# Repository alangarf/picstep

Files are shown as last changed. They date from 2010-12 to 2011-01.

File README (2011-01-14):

Firstly thanks for looking at my design, it was started from the ground up for
the community to share and use. I've released all code and designs under GPL,
which means it's free to use for any purpose as long as my copyright is
retained and any modifications are also released publicly. Any commercial
interest must be approved by ME! :)

PICStep is a micro-stepping step motor controller that uses a special set of
driver ICs (LMD18245) to control the motor coils current to such a degree that
you can divide the magnetic steps of a step motor to 1/2, 1/4, 1/8th or even 1/16th
their original size! Of course resolution suffers a little in 1/16th mode as not
all steps are mechanically identical from one to another; the difference
is negligible, but the increased smoothness and efficiency is dramatic!

PICStep uses a single layer board and about 30 components and a few wire links
to make it all happen.

The LMD18245 are rated at 55V @ 3amps but I've not tested it up to that range
and there are special requirements that need to be met to deal with back EMF
at this range. I'd suggest reading the LMD18245 data-sheet (which is available
freely on the net') if you wish to use these drivers at or near this voltage.

I've tested PICStep at 40VDC @ 2.5A without any modification or problems, but your
mileage may vary! :)

I use a simple 24V toroidal transformer and bridge rectifier for my PSU. 24V
RMS works out to about 35VDC when rectified. Plus I've provided massive amounts
of filtering by using a very large electrolytic capacitor to filter out the humps
and bumps. It works very well and can supply my three drivers without a problem.

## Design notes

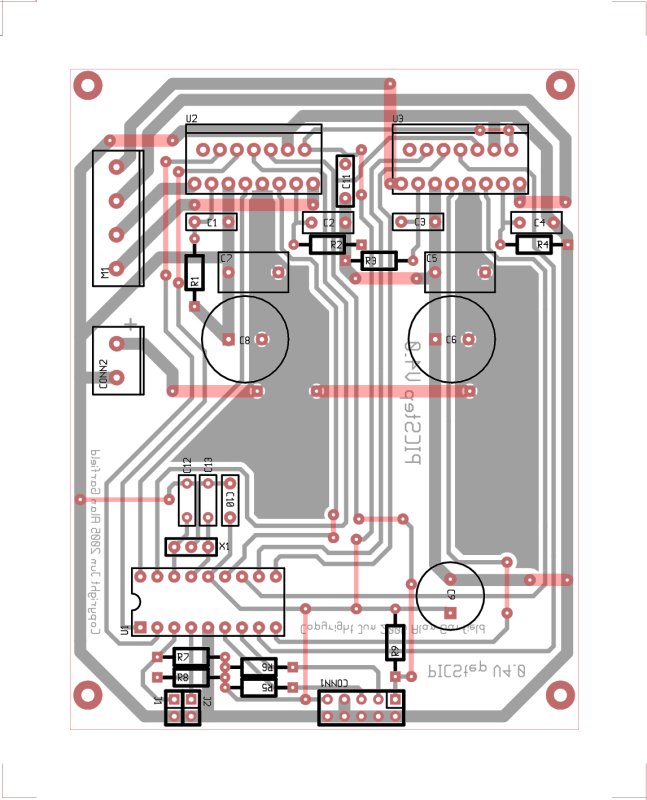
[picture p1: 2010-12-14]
v4.0/picstep_v4_0_overlay.jpg

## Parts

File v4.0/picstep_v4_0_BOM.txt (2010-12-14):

Resistors
-------------

5 x 10K 1/4W (R5, R6, R7, R8, R9)			RR-0596
2 x 20K 1/4W (R1, R3)					RR-0603
2 x 20K 1/4W (R2, R4) - Adjustable to set current limit read readme

Capacitors
-------------

2 x 2.2nF MKT (C1, C3)					RM-7022	
2 x 500pF Ceramic (C2, C4)				RC-5333
2 x 1uF 100V MKT (C5, C7)				RM-7170
2 x 470uF 63V Electro (C6, C8)				RE-6210
1 x 100uF 16V Electro (C9)				RE-6130
2 x 10nF MKT (C10, C11)					RM-7065
2 x 2pF MKT/Ceramic (C12, C13) (Only needed if you are using a XTAL)

Semiconductors
-------------

1 x PIC16F628A (U1)					ZZ-8520
2 x LMD18245 (U2, U3)					DIGIKEY LMD18245T-ND

Misc
-------------

1 x 10 pin IDC header (CONN1)
2 x 2 pin IDC headers (J1, J2)
3 x 2 way PCB Mount Screw Terminal (CONN2, M1 x 2)	HM-3172
1 x 20MHz 3 pin resonator (X1)				Dontronics ZTT-20.00MX

X1 can be replaced with a 20MHz XTAL, if this is the case make sure to use
appropriate sized capacitors in C12 and C13. With a resonators these
capacitors aren't needed!

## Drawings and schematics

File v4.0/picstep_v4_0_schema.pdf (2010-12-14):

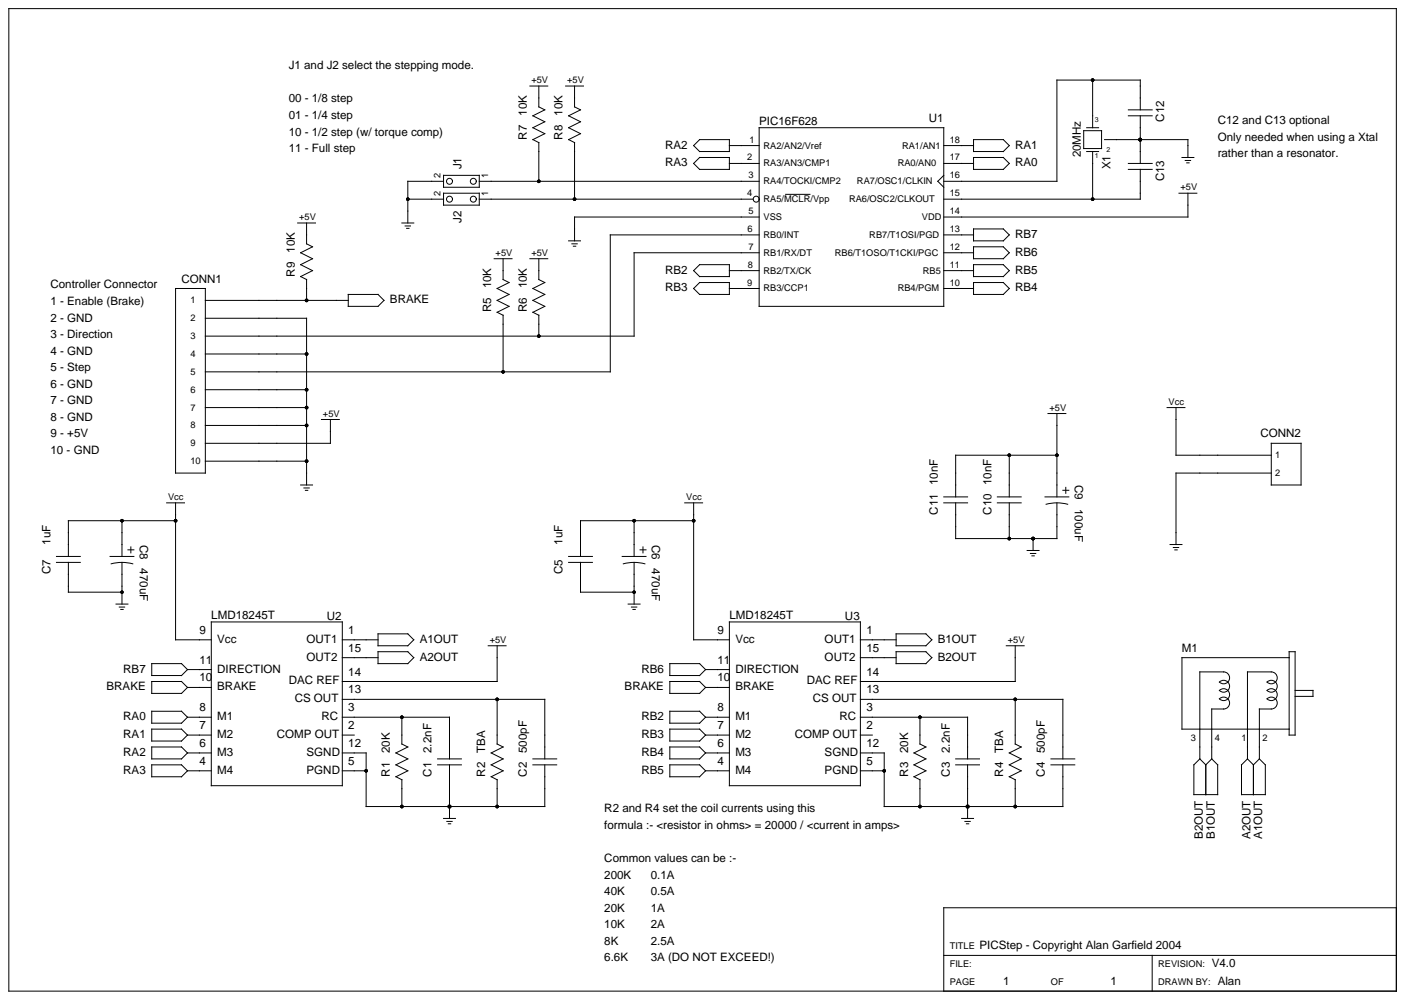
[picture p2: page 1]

J1 and J2 select the stepping mode.

C12 C13 C12 and C13 optional Only needed when using a Xtal rather than a resonator.

R2 and R4 set the coil currents using this
formula :- <resistor in ohms> = 20000 / <current in amps>

Common values can be :-

PICStep - Copyright Alan Garfield 2004
TITLE

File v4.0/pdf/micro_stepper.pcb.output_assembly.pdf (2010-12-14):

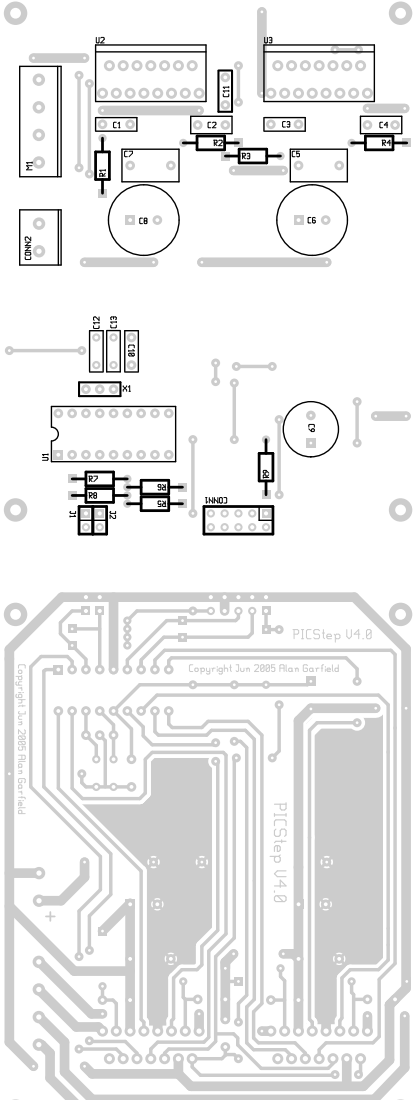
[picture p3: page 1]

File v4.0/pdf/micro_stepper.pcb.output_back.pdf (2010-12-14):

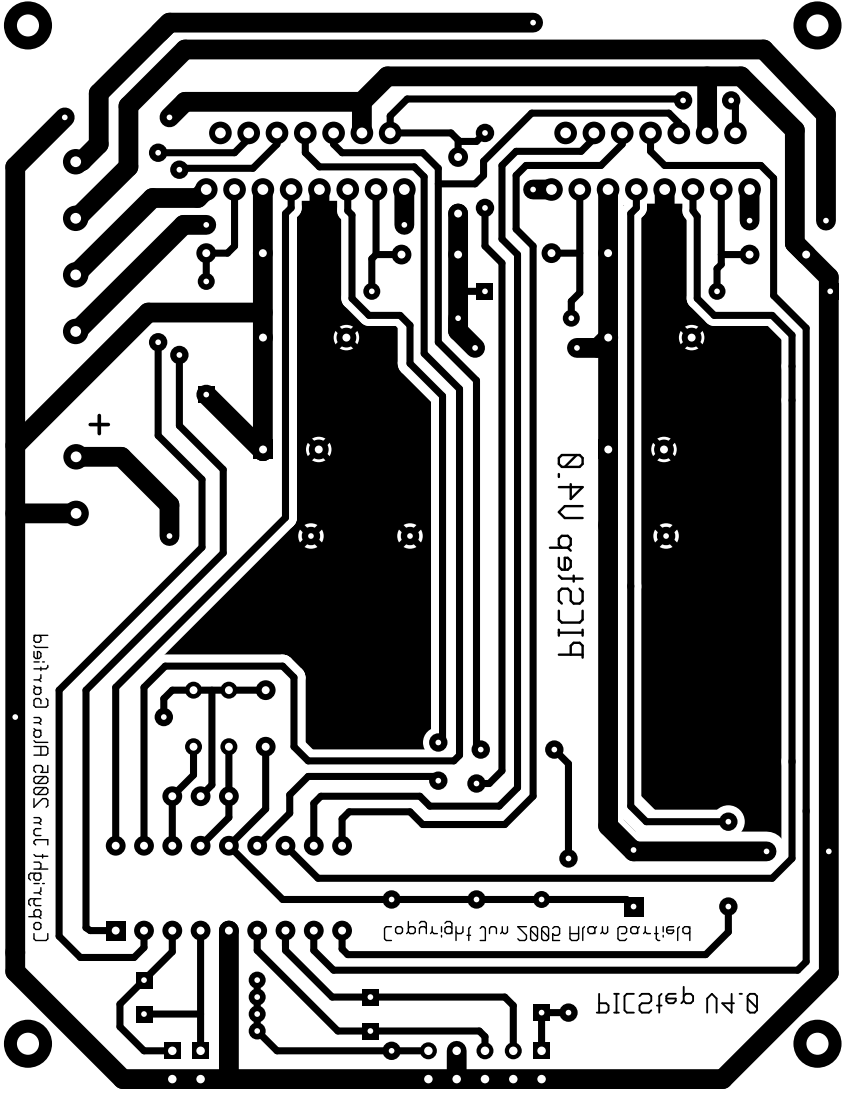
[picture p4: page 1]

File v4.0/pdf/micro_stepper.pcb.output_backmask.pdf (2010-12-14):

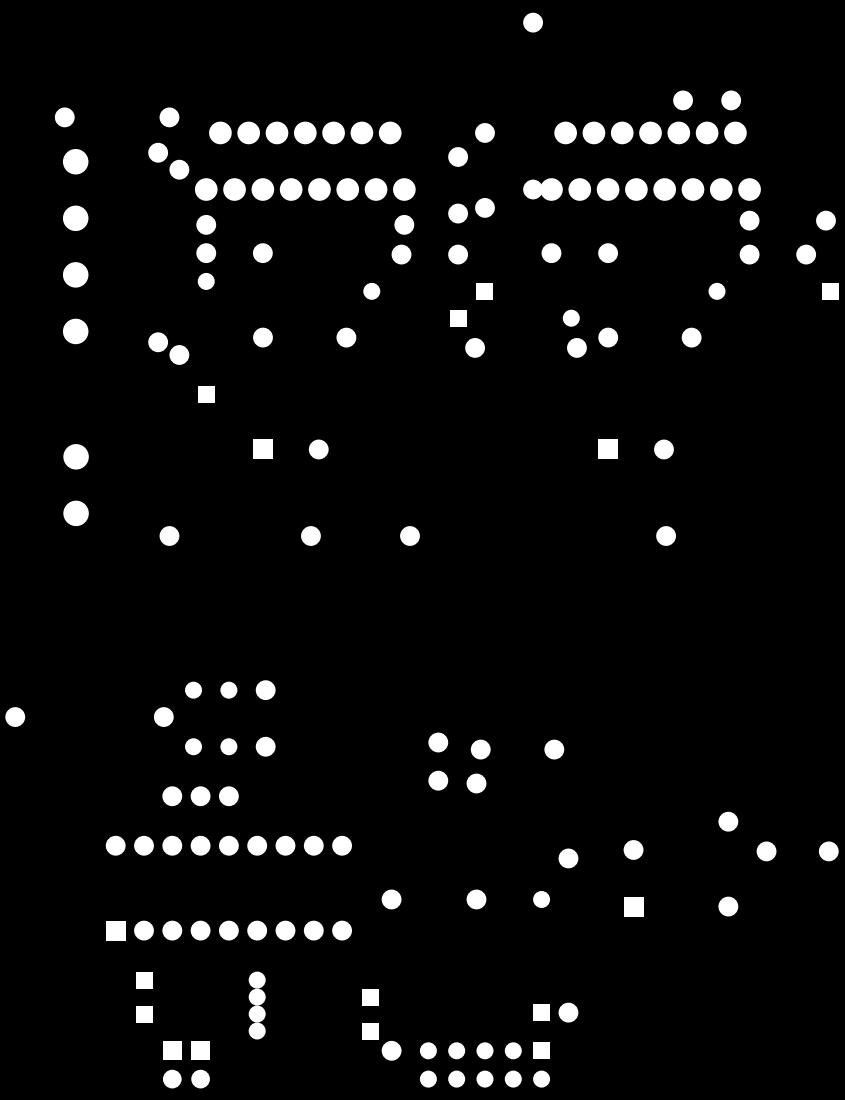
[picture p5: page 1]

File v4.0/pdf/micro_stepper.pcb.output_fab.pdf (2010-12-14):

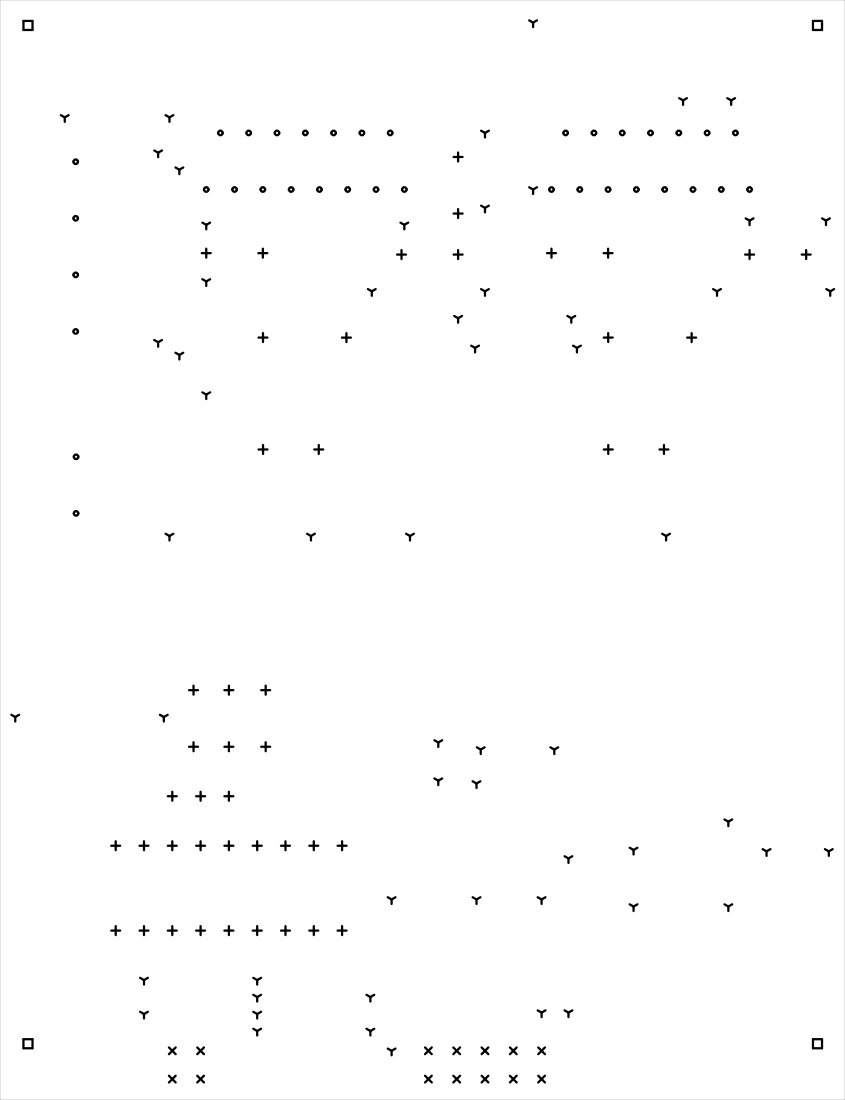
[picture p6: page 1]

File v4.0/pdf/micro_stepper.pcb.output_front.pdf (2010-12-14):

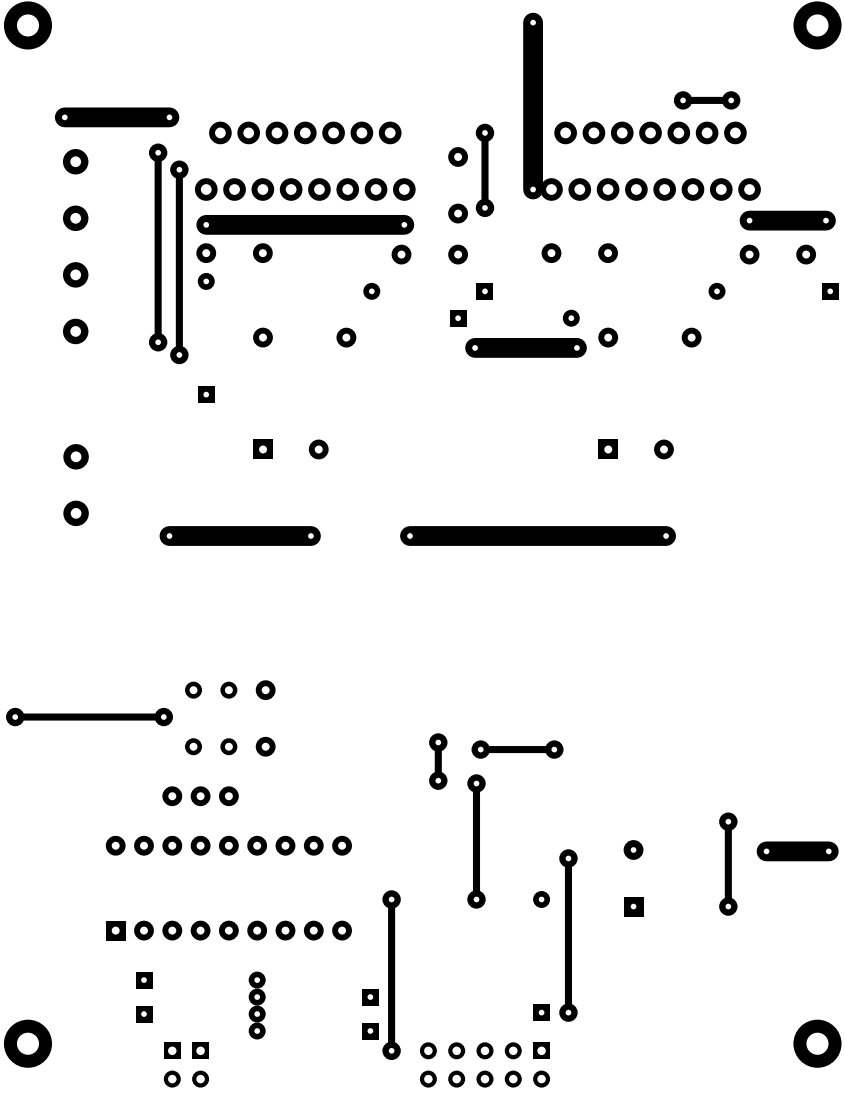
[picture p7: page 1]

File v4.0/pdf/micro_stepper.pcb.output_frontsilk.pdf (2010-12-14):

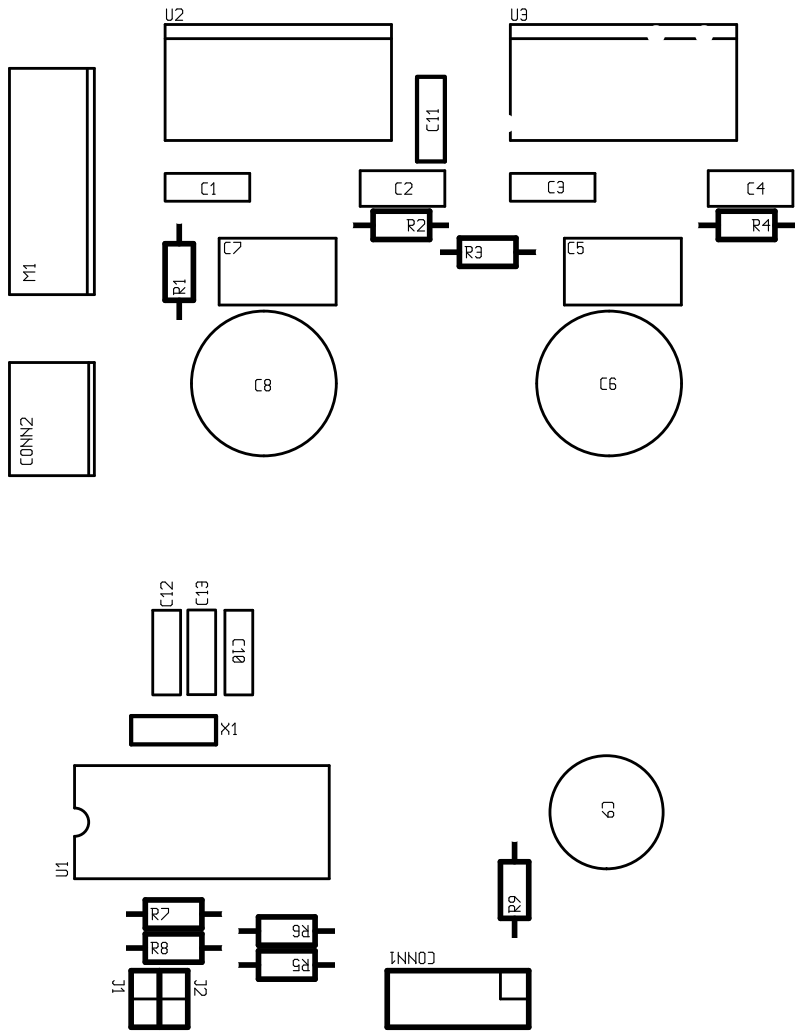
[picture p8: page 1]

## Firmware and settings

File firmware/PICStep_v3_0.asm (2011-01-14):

; PICStep v3.0 Firmware - PIC based microstepping motor controller
; Copyright (C) 2004-2011 Alan Garfield <alan@fromorbit.com>

; This program is free software; you can redistribute it and/or
; modify it under the terms of the GNU General Public License
; as published by the Free Software Foundation; either version 2
; of the License, or (at your option) any later version.

; This program is distributed in the hope that it will be useful,
; but WITHOUT ANY WARRANTY; without even the implied warranty of
; MERCHANTABILITY or FITNESS FOR A PARTICULAR PURPOSE.  See the
; GNU General Public License for more details.

; You should have received a copy of the GNU General Public License
; along with this program; if not, write to the Free Software
; Foundation, Inc., 59 Temple Place - Suite 330, Boston, MA  02111-1307, USA.

 title "PICStep V3.0"

  LIST R=DEC
  #define __16F628a
  #include p16f628a.inc

; MODE PINS
; RA4 - Selects between the two micro-stepping modes below
; RA5 - Turns timeout function on/off

; ========== FIRMWARE SETTINGS ==========

; === TIMEOUT TIME ===
; Uncomment only ONE!

;  #define TIMEOUT_TIME 1	; ~3 mins
;  #define TIMEOUT_TIME 2	; ~6 mins
;  #define TIMEOUT_TIME 3	; ~12 mins
  #define TIMEOUT_TIME 4	; ~24 mins
;  #define TIMEOUT_TIME 5	; ~48 mins
;  #define TIMEOUT_TIME 6	; ~1 hour 36 mins
;  #define TIMEOUT_TIME 7	; ~3 hours 12 mins

; === CURRENT REDUCE 50% MODE ===
; Uncomment if you want a 50% reduction or
; leave commented for a full reduction

  #define FIFTY_PERCENT

; === MICRO-STEPPING MODES ===
; Uncomment only TWO!

  #define MICRO_16 ; 1/16
  #define MICRO_8 ; 1/8
;  #define MICRO_4 ; 1/4
;  #define MICRO_2 ; 1/2
;  #define MICRO_1 ; Full

; ========== NO CHANGES REQUIRED BELOW ==========

; Registers
  UDATA 0x020
step            RES 1
portA_shadow    RES 1
mode            RES 1
lookup          RES 1
temp            RES 1
timeout_reg     RES 1
timeout         RES 2

_w              RES 1
_status         RES 1
_fsr            RES 1
_pclath         RES 1

 __CONFIG _CP_OFF & _WDT_ON & _HS_OSC & _PWRTE_ON & _LVP_OFF & _MCLRE_OFF
  org       0
  goto      Mainline        ; Main line vector

  org 4
  goto      Interupt        ; Interupt vector

  CODE
Interupt
; Save Current Context
    movwf       _w
    movf        STATUS, w
    bcf         STATUS, RP1
    bcf         STATUS, RP0
    movwf       _status
    movf        FSR, w
    movwf       _fsr
    movf        PCLATH, w
    movwf       _pclath
    clrf        PCLATH

; Interrupt service routine
    btfsc       INTCON, INTF
      call INTB0                ; Call INTBO interrupt handler

    btfsc       PIR1, TMR2IF
      call TIMEOUT              ; Call TIMEOUT interrupt handler

; Reset Current Context
    movf        _pclath, w
    movwf       PCLATH
    movf        _fsr, w
    movwf       FSR
    movf        _status, w
    movwf       STATUS
    swapf       _w, f
    swapf       _w, w
    retfie

INTB0
; Handle interupt on RB0

    clrf        timeout         ; Reset timeout timer and register
    clrf        timeout + 1
    clrf        timeout_reg

; Advance the index position
    movlw       HIGH MODE_TABLE
    movwf       PCLATH
    movf        mode, w         ; Load the current mode
    call        MODE_TABLE      ; Get the advance value for this mode
    movwf       lookup          ; Store it for later

    btfss       PORTB, 1        ; Check on the direction pin (RB1)
      goto      $ + 4           ; Jump over step addition

    addwf       step, w         ; Add the current mode to the current position value
    movwf       step            ; Update step
    goto        $ + 3           ; Jump over step subtraction

    subwf       step, w         ; Subtract the current mode from the current position value
    movwf       step            ; Update step

; Bounds check the table
    movlw       0x040           ; Check if step has overflowed the edge of the table
    subwf       step, w
    btfsc       STATUS, Z
      clrf      step

    movf        lookup, w       ; Check if step has underflowed the edge of the table
    sublw       0x040
    subwf       step, w
    btfsc       STATUS, C
      subwf     step, f

; Process DAC A
    movlw       HIGH STEP_TABLE_A
    movwf       PCLATH
    movf        step, w         ; Reload step into w
    call        STEP_TABLE_A    ; Get the result from the table
    movwf       lookup          ; Store the fetched results for later

    btfss       PORTB, 1        ; Check on the direction pin (RB1)
      rlf       lookup, w       ; Rotate to the alternate direction bit to fix a bug in LMD

    xorwf       PORTB, w        ; Prepare the direction bit for DAC A
    andlw       B'10000000'     ; Mask out the direction bit
    xorwf       PORTB, f        ; Output the direction bit

    movf        lookup, w       ; Reload the fetched table results

    andlw       B'00001111'     ; Mask out the upper nibble
    movwf       PORTA           ; Output the DAC results for A

; Process DAC B
    movlw       HIGH STEP_TABLE_B
    movwf       PCLATH
    movf        step, w         ; Reload step into w
    call        STEP_TABLE_B    ; Get the result from the table
    movwf       lookup          ; Store the fetched results for later

    btfss       PORTB, 1        ; Check on the direction pin (RB1)
      rlf       lookup, w       ; Rotate to the alternate direction bit to fix a bug in LMD

    xorwf       PORTB, w        ; Prepare the direction bit for DAC B
    andlw       B'01000000'     ; Mask out the direction bit
    xorwf       PORTB, f        ; Output the direction bit

    rlf         lookup, f       ; Rotate lookup left in place
    rlf         lookup, w       ; Rotate again but into WREG

    xorwf       PORTB, w
    andlw       B'00111100'     ; Mask out the not needed bits
    xorwf       PORTB, f        ; Output the DAC results for B

    bcf         INTCON, INTF    ; Clear RB0 Interrupt flag
    return

TIMEOUT
; Handle motor timeout TMR2 interrupt and return ASAP

    bsf         timeout_reg, 7  ; Set the timeout bit so the count can increment
    bcf         PIR1, TMR2IF    ; Clear TMR2 Interrupt flag
    return

Mainline

; Initialize Variables

    clrf        step
    clrf        mode
    clrf        lookup
    clrf        timeout
    clrf        timeout + 1
    clrf        timeout_reg
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
